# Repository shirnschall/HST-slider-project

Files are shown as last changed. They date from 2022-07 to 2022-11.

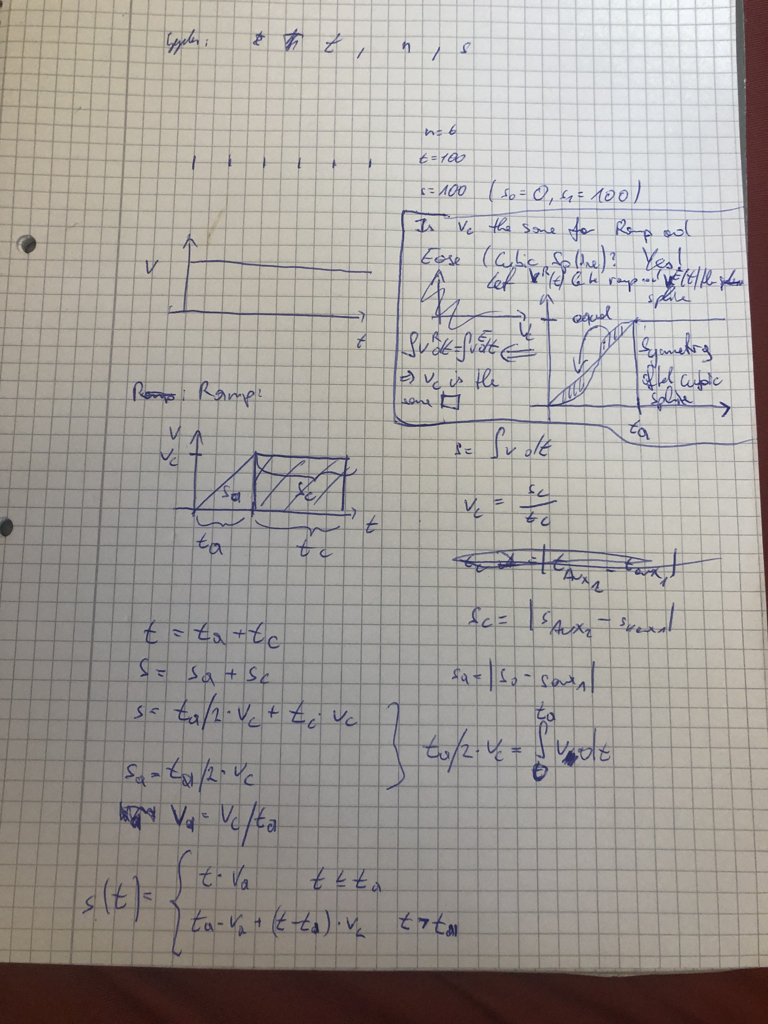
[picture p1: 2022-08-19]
notes-sketches-other-thoughts/non-constant-slider-motion.JPG

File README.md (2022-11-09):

# hs-slider-project
Combining 3d printed and metal parts to build an open source motorized dslr slider.

### More Details
You can find more inforamtion about important features, and how this project was designed in this projects blog post at [https://blog.hirnschall.net/diy-motorized-slider/](https://blog.hirnschall.net/diy-motorized-slider/)

### IMPORTANT NOTE: 
Known issues for pcb v1.0:
- Due to an issue with the current pcb design v1.0 (missing trace), it is required to solder the MS1_PIN to the MS2_PIN on the A4988 stepper driver, to get 8x and 16x micro-stepping working. These pins are labeled on the slider-controller pcb.
- The pinout of the 3.3V regulator ist not correct. The 5V IN and the 3.3V OUT pins have to be swaped. The correct pinout of the pcb is as shown here https://github.com/shirnschall/hs-slider-project/blob/master/schematics/board.pdf

Sorry for the inconvenience!

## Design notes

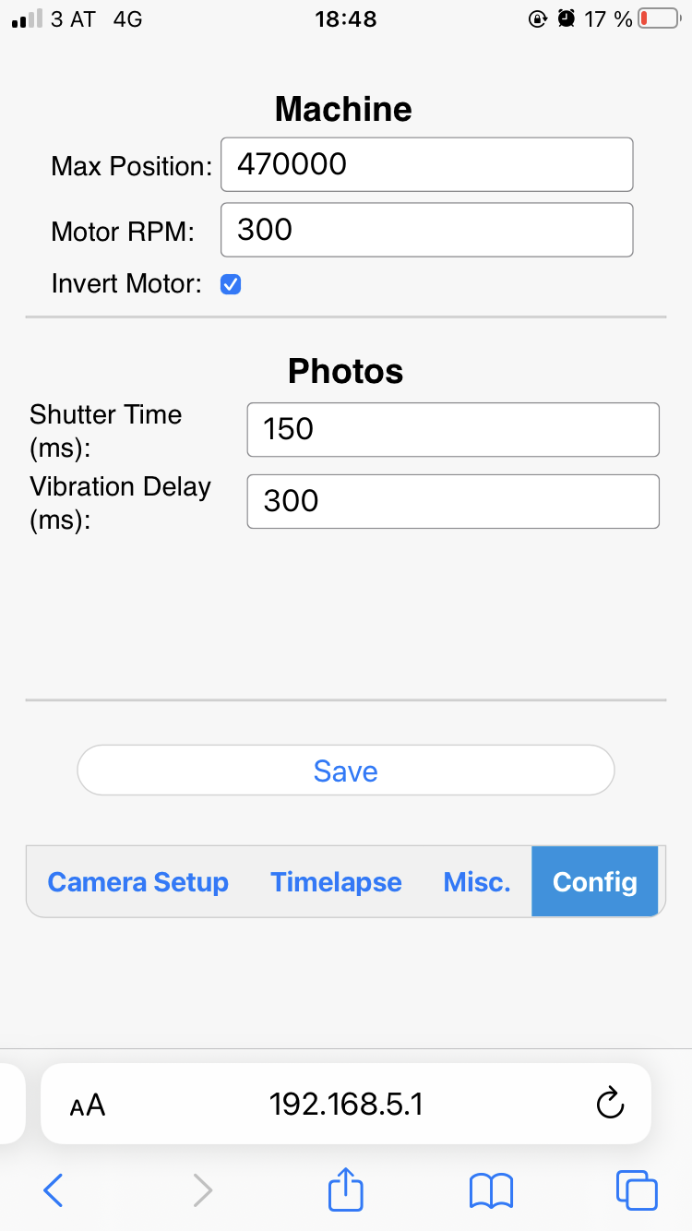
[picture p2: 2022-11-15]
slider-firmware/default-settings.PNG

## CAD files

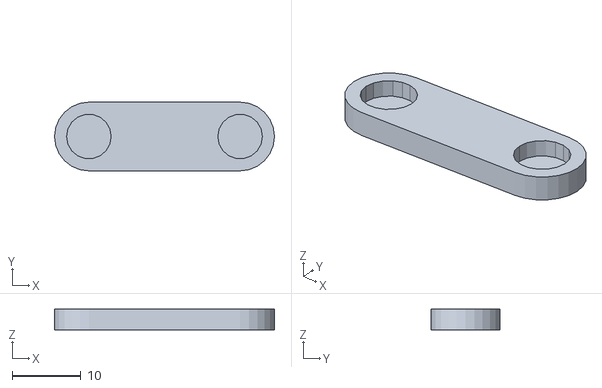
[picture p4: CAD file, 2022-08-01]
stl/belt-mount.stl
32.0 x 10.0 x 3.00

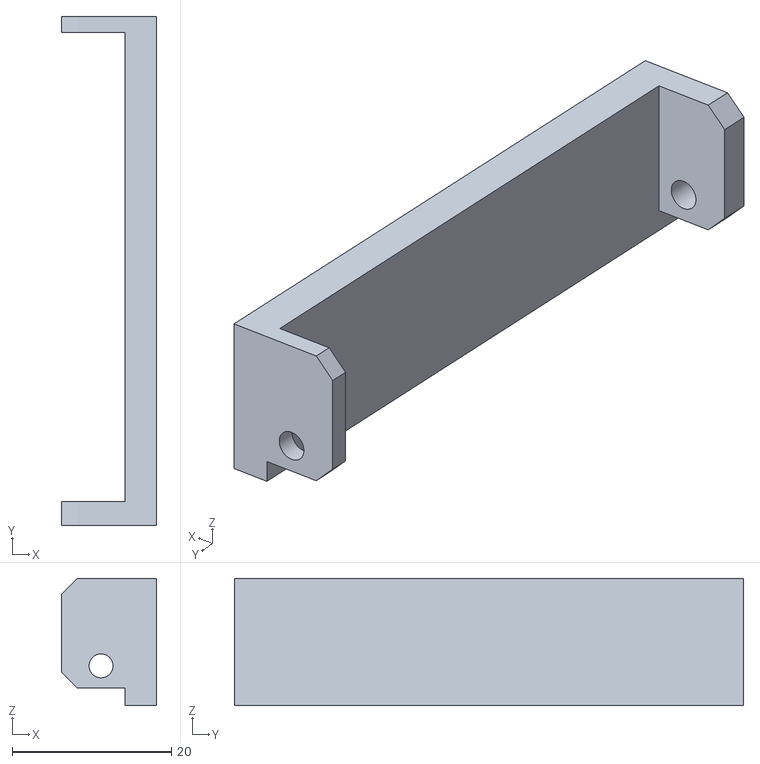
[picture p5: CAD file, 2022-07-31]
stl/pcb-cover.stl
12.0 x 64.0 x 16.0

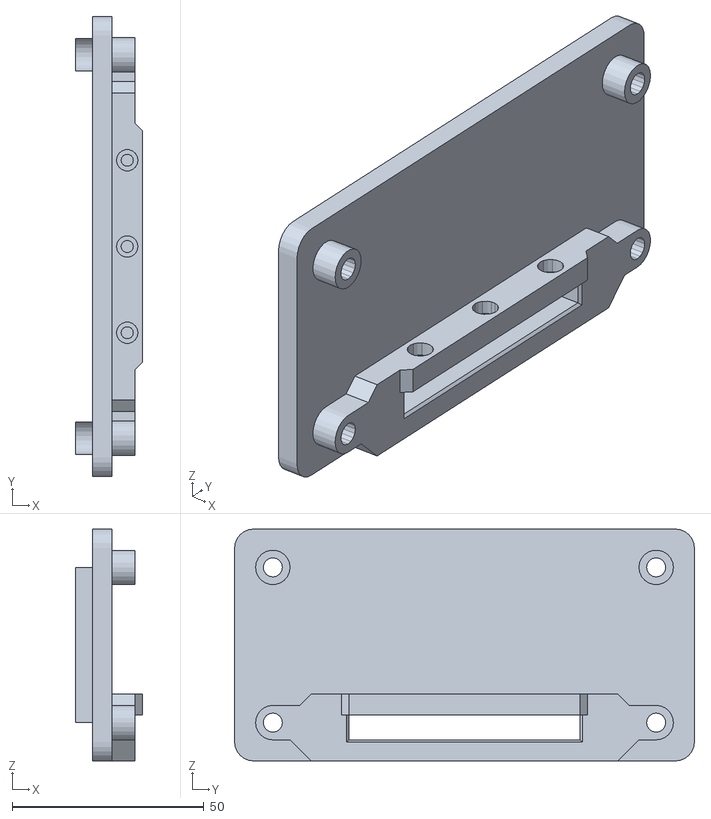
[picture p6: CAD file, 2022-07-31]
stl/tripod-gantry-side.stl
17.5 x 120.0 x 60.5

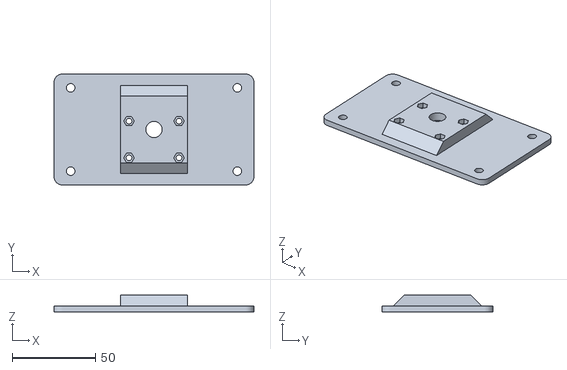
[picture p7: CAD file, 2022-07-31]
stl/cam-gantry-bottom.stl
120.0 x 66.5 x 10.0

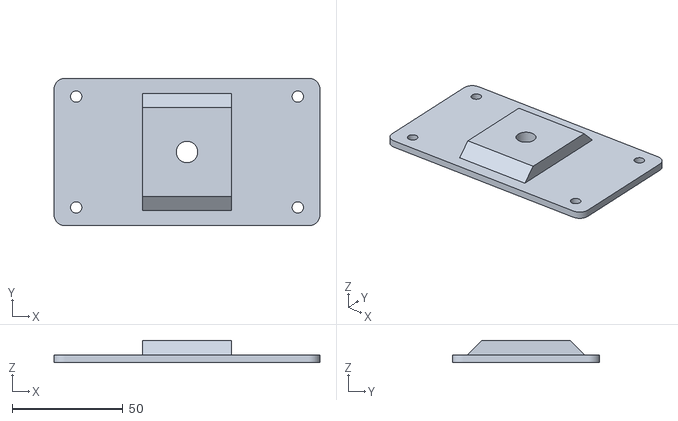
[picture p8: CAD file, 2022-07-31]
stl/cam-gantry-top.stl
120.0 x 66.5 x 10.0

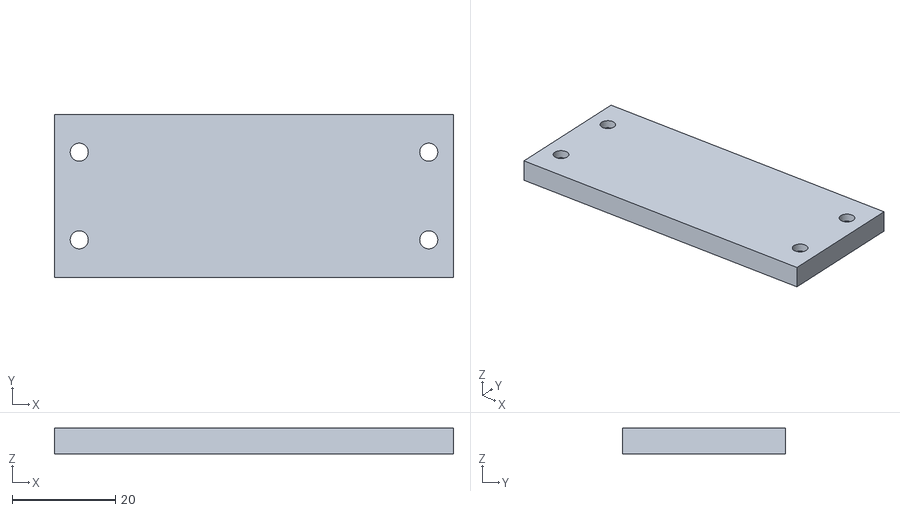
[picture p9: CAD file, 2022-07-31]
stl/idler-cover.stl
77.4 x 31.6 x 5.00

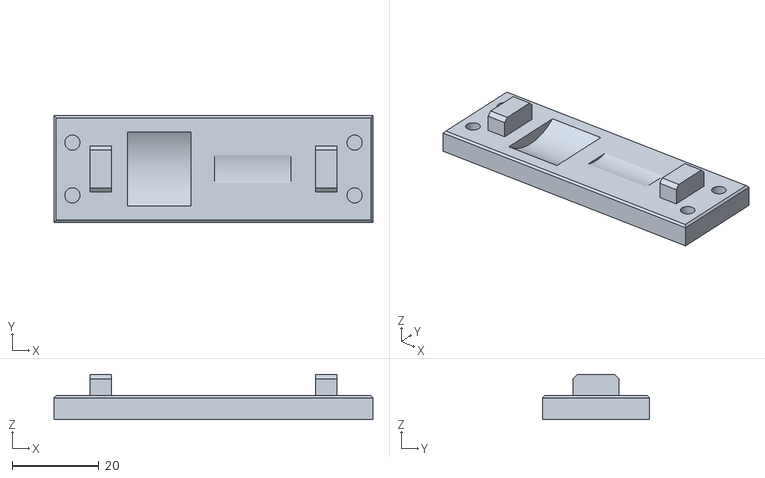
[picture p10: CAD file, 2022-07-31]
stl/motor-end-cover.stl
73.5 x 24.6 x 10.4

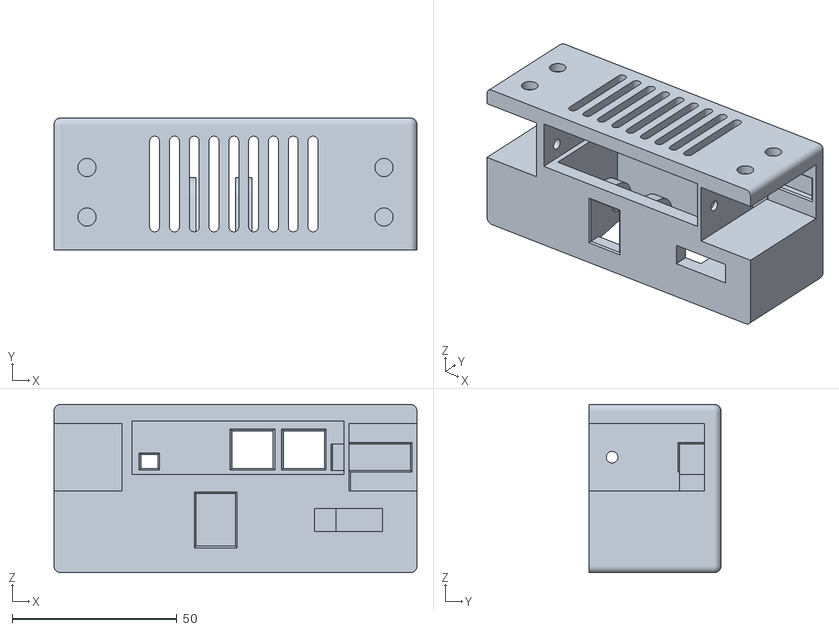
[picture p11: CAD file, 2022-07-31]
stl/pcb-end.stl
110.0 x 40.0 x 51.0

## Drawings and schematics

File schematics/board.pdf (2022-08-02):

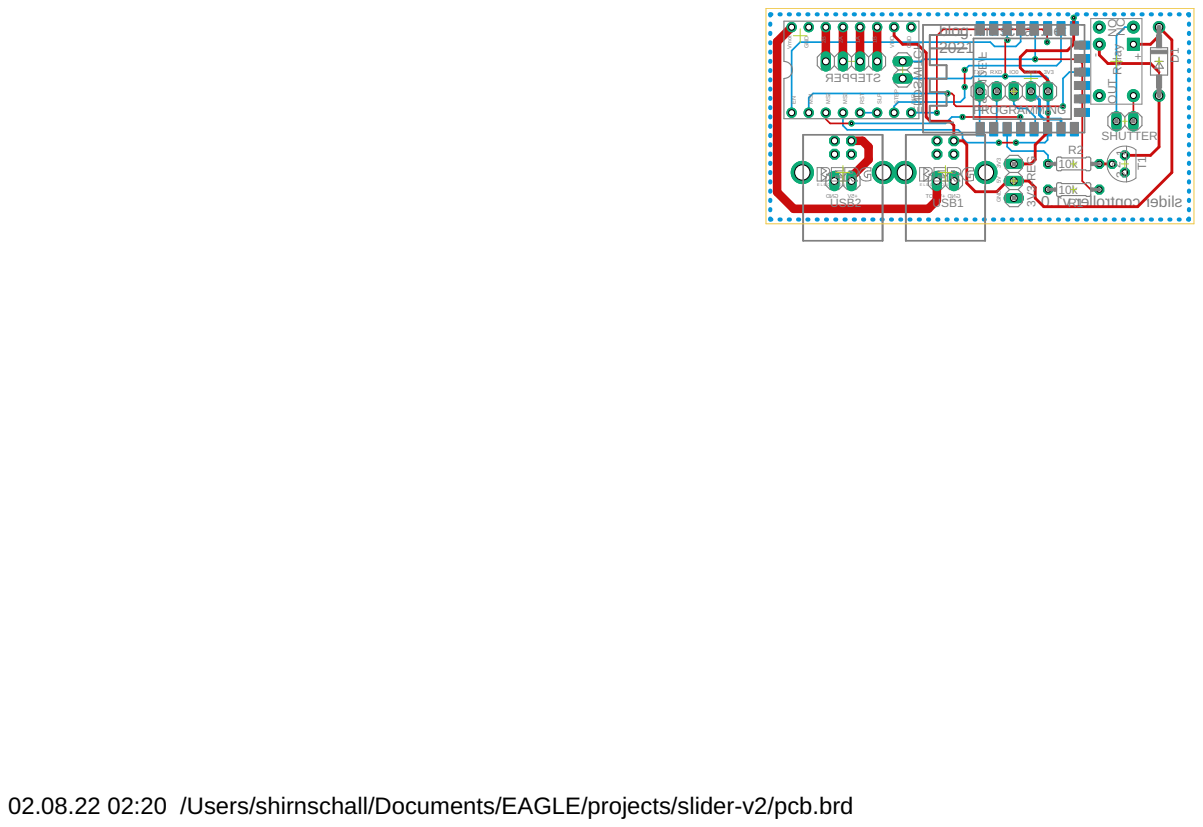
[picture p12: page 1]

02.08.22 02:20 /Users/shirnschall/Documents/EAGLE/projects/slider-v2/pcb.brd

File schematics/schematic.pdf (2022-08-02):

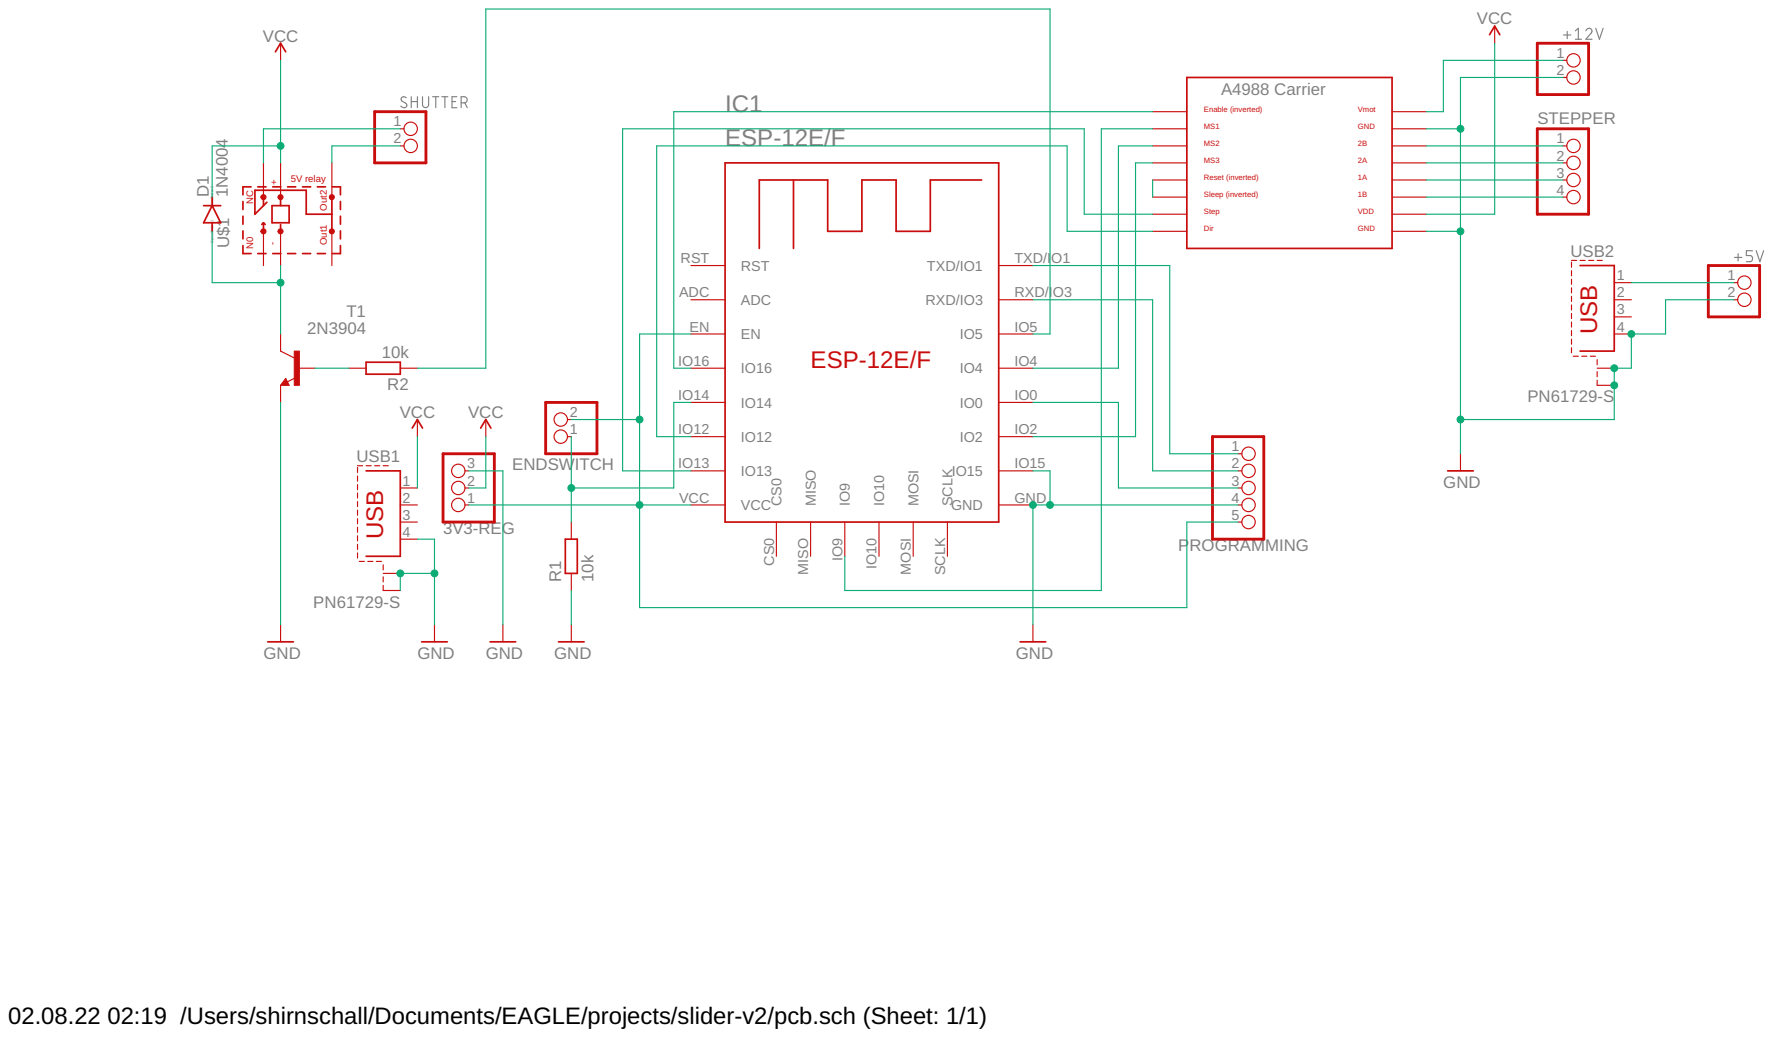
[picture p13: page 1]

02.08.22 02:19 /Users/shirnschall/Documents/EAGLE/projects/slider-v2/pcb.sch (Sheet: 1/1)

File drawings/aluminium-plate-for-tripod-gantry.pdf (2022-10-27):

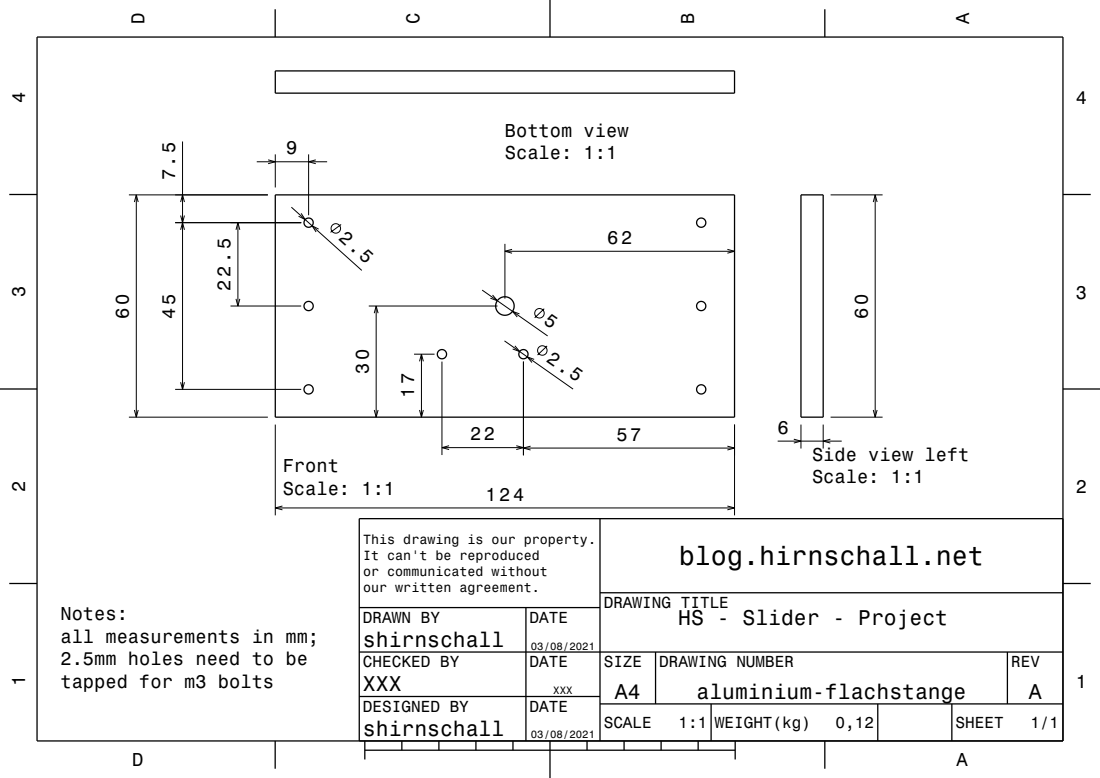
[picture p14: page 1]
Scale: 1:1; Side view left Scale: 1:1; Bottom view Scale: 1:1

This drawing is our property.
It can't be reproduced
or communicated without
our written agreement.

blog.hirnschall.net

DRAWING TITLE
HS - Slider - Project

Notes:
all measurements in mm;
2.5mm holes need to be
tapped for m3 bolts

DRAWN BY shirnschall | DATE 03/08/2021

CHECKED BY XXX | DATE XXX | SIZE A4 | DRAWING NUMBER aluminium-flachstange | REV A

DESIGNED BY shirnschall | DATE 03/08/2021

SCALE 1:1 | WEIGHT(kg) 0,12 | SHEET 1/1

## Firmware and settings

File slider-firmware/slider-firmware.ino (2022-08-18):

#include <EEPROM.h>
//---------------------------------------------------
#include <ESP8266WiFi.h>
const char *ssid = "HS-Slider";
const char *password = "Sebastian012";
IPAddress localIp(192,168,5,1);
IPAddress gateway(192,168,5,1);
IPAddress subnet(255,255,255,0);
//---------------------------------------------------
#include <ESP8266WebServer.h>
ESP8266WebServer server(80);  //listen to port 80
//---------------------------------------------------
#include <Arduino.h>
#include "BasicStepperDriver.h"
// Motor steps per revolution. Most steppers are 200 steps or 1.8 degrees/step
#define MOTOR_STEPS 200
//#define motorRpm 250
#define stepperDir_PIN 12
#define STEPPER_STEP_PIN 13
#define MICROSTEPS 8
#define MS1_PIN 9
#define MS2_PIN 4
#define MS3_PIN 2
#define STEPPER_EN_PIN 16
BasicStepperDriver stepper(MOTOR_STEPS, stepperDir_PIN, STEPPER_STEP_PIN);

//#define shutterDelay 100 //time for the ralay to open
#define RELAY_PIN 5
//#define vibrationDelay 300 //in ms

#define ENDSTOP_PIN 14
//#define stepperDir -1 //-1 or 1 to change direction
//#define maxPos 440000  //in steps
#define HOMING_SPEED 5


//minified with https://kangax.github.io/html-minifier/
//use option "Case sensitive" and disable "remove optional tags", and "remove tag whitespace"
const char index_html[] PROGMEM = R"rawliteral(<!doctype html><html lang="en"><head><link rel="manifest" href="/manifest.webmanifest"><script type="text/javascript">var width=screen.width,meta=document.createElement("meta");meta.name="viewport",meta.content=width<600?"width=device-width,initial-scale="+width/540:"width=device-width,initial-scale=1",document.getElementsByTagName("head")[0].appendChild(meta)</script><style>.slidecontainer{margin:auto;transition:color .2s ease-in-out}.slidecontainer input{position:relative;width:200px;margin:0 10px 0 10px}input{font-size:18pt!important}.slidecontainer button{width:60px;height:40px;background:#fff;font-size:24px;border:1px solid #d3d3d3;cursor:pointer;-webkit-appearance:none;margin:0}body{font-size:16pt;font-family:sans-serif}.start-stop{width:420px;height:40px;border-radius:20px;background:#fff;font-size:24px;border:1px solid #d3d3d3;cursor:pointer;-webkit-appearance:none;margin:10px 10px}.config{width:200px;height:40px;border-radius:20px;background:#fff;font-size:24px;border:1px solid #d3d3d3;cursor:pointer;-webkit-appearance:none;margin:10px 10px}button:hover:enabled{background-color:#0094e2;color:#fff}.heading{text-align:center;font-size:20pt;font-weight:700}td{text-align:center}.slider-l{border-bottom-left-radius:20px;border-top-left-radius:20px}.slider-r{border-bottom-right-radius:20px;border-top-right-radius:20px}#container{width:500px;margin:auto;text-align:center;padding:20px 10px 0 10px}table{margin:auto;padding-top:10px}body,html{margin:0;padding:0;width:100%;height:100%;background-color:#f7f7f7}button{touch-action:manipulation}.slider{width:200px;margin:0 10px}.tab{margin-top:20.667px;padding:0;border-radius:0 0 15px 15px;overflow:hidden;border:1px solid #ccc;background-color:#f1f1f1}.tab button{margin:0;font-size:16pt;background-color:inherit;float:left;border:none;outline:0;cursor:pointer;padding:14px 16px;transition:.3s;font-weight:700}.tab button:hover{background-color:#ddd;color:#000}.tab button.active{background-color:#0094e2;color:#fff}.tabcontent{display:none;padding:6px 0;border-top:none;position:relative}.buttonTableContainer{position:absolute;bottom:-20px;width:100%}.buttonTable{width:450px;margin:25px;margin-top:0}.alignL{text-align:left}hr{border:1px solid #ccc}</style></head><body><div id="container"><div id="setup" class="tabcontent"><div class="slidecontainer"><table><tr class="heading"><td colspan="3">Start Position</td></tr><tr><td><button class="slider-l" id="slider-minus-big-1">-5</button><button class="slider-r" id="slider-minus-1">-1</button></td><td><input type="range" min="0" max="100" value="0" class="slider" id="slider-1"></td><td><button class="slider-l" id="slider-plus-1">+1</button><button class="slider-r" id="slider-plus-big-1">+5</button></td></tr><tr><td></td><td><center><div class="slider-value" id="slider-value-1">16</div></center></td><td></td></tr></table></div><hr><div class="slidecontainer"><table><tr class="heading"><td colspan="3">End Position</td></tr><tr><td><button class="slider-l" id="slider-minus-big-2">-5</button><button class="slider-r" id="slider-minus-2">-1</button></td><td><input type="range" min="0" max="100" value="100" class="slider" id="slider-2"></td><td><button class="slider-l" id="slider-plus-2">+1</button><button class="slider-r" id="slider-plus-big-2">+5</button></td></tr><tr><td></td><td><center><div class="slider-value" id="slider-value-2">16</div></center></td><td></td></tr></table></div><hr><div class="slidecontainer"><table><tr class="heading"><td colspan="3">Current Position</td></tr><tr><td><button class="slider-l" id="slider-minus-big-3" onclick="goToMinus(10)">-10</button><button class="slider-r" id="slider-minus-3" onclick="goToMinus(1)">-1</button></td><td><progress id="slider-3" value="32" max="100" class="slider"></progress></td><td><button class="slider-l" id="slider-plus-3" onclick="goToPlus(1)">+1</button><button class="slider-r" id="slider-plus-big-3" onclick="goToPlus(10)">+10</button></td></tr><tr><td></td><td><center><div class="slider-value" id="slider-value-3">16</div></center></td><td></td></tr></table></div><hr><table><tr><td><button class="config" id="gotostart" onclick="goToStart()">Go to Start</button></td><td><button class="config" id="gotoend" onclick="goToEnd()">Go to End</button></td></tr><tr><td><button class="config" id="home" onclick="home()">Home</button></td><td><button class="config" id="takephoto" onclick="takePhoto()">Take Photo</button></td></tr></table></div><div id="timelapse" class="tabcontent"><div class="buttonTableContainer"><table><tr><td><label for="duration">Duration (s):</label></td><td><input type="number" inputmode="numeric" pattern="[0-9]*" id="duration" name="duration"></td></tr><tr><td><label for="noPics">No. Pictures:</label></td><td><input type="number" inputmode="numeric" pattern="[0-9]*" id="noPics" name="noPics"></td></tr></table><hr><table class="buttonTable"><tr><td colspan="2"><button class="start-stop" id="start" onclick="startJob()">Start</button></td></tr></table></div></div><div id="misc" class="tabcontent" style="color:rgba(16,16,16,.3)"><table><tr class="heading"><td colspan="3">Motion Type</td></tr><tr><td class="alignL"><input type="radio" name="motionType" checked value="linear" id="linear" onchange="updateAuxiliarySliders(-1)" disabled><label for="linear">Constant</label></td><td></td><td></td></tr><tr><td class="alignL"><input type="radio" name="motionType" value="easeInOut" id="easeInOut" onchange="updateAuxiliarySliders(2)" disabled><label for="easeInOut">Ease in/out</label></td><td class="alignL"><input type="radio" name="motionType" value="easeIn" id="easeIn" onchange="updateAuxiliarySliders(0)" disabled><label for="easeIn">Ease in</label></td><td class="alignL"><input type="radio" name="motionType" value="easeOut" id="easeOut" onchange="updateAuxiliarySliders(1)" disabled><label for="easeOut">Ease out</label></td></tr><tr><td class="alignL"><input type="radio" name="motionType" value="rampInOut" id="rampInOut" onchange="updateAuxiliarySliders(2)" disabled><label for="rampInOut">Ramp in/out</label></td><td class="alignL"><input type="radio" name="motionType" value="rampIn" id="rampIn" onchange="updateAuxiliarySliders(0)" disabled><label for="rampIn">Ramp in</label></td><td class="alignL"><input type="radio" name="motionType" value="rampOut" id="rampOut" onchange="updateAuxiliarySliders(1)" disabled><label for="rampOut">Ramp out</label></td></tr></table><hr><div class="slidecontainer" id="auxiliarySliderContainer0"><table><tr class="heading"><td colspan="3">Auxiliary Point (in)</td></tr><tr><td><button class="slider-l" id="slider-minus-big-4">-5</button><button class="slider-r" id="slider-minus-4">-1</button></td><td><input type="range" min="0" max="100" value="20" class="slider" id="slider-4"></td><td><button class="slider-l" id="slider-plus-4">+1</button><button class="slider-r" id="slider-plus-big-4">+5</button></td></tr><tr><td></td><td><center><div class="slider-value" id="slider-value-4">20</div></center></td><td></td></tr></table></div><hr><div class="slidecontainer" id="auxiliarySliderContainer1"><table><tr class="heading"><td colspan="3">Auxiliary Point (out)</td></tr><tr><td><button class="slider-l" id="slider-minus-big-5">-5</button><button class="slider-r" id="slider-minus-5">-1</button></td><td><input type="range" min="0" max="100" value="80" class="slider" id="slider-5"></td><td><button class="slider-l" id="slider-plus-5">+1</button><button class="slider-r" id="slider-plus-big-5">+5</button></td></tr><tr><td></td><td><center><div class="slider-value" id="slider-value-5">80</div></center></td><td></td></tr></table></div><div class="buttonTableContainer"><hr><table class="buttonTable"><tr><td colspan="2"><button class="start-stop" id="start" onclick="startJob()" disabled>Start</button></td></tr></table></div></div><div id="config" class="tabcontent"><table><tr class="heading"><td colspan="2">Machine</td></tr><tr><td class="alignL"><label for="maxPos">Max Position:</label></td><td><input type="number" inputmode="numeric" pattern="[0-9]*" id="maxPos" name="maxPos"></td></tr><tr><td class="alignL"><label for="rpm">Motor RPM:</label></td><td><input type="number" inputmode="numeric" pattern="[0-9]*" id="rpm" name="rpm"></td></tr><tr><td class="alignL"><label for="invertMotor">Invert Motor:</label></td><td class="alignL"><input type="checkbox" id="invertMotor" name="invertMotor"></td><td></td></tr></table><hr><table><tr class="heading"><td colspan="2">Photos</td></tr><tr><td class="alignL"><label for="shutter">Shutter Time (ms):</label></td><td><input type="number" inputmode="numeric" pattern="[0-9]*" id="shutter" name="shutter"></td></tr><tr><td class="alignL"><label for="vibration">Vibration Delay (ms):</label></td><td><input type="number" inputmode="numeric" pattern="[0-9]*" id="vibration" name="vibration"></td></tr></table><div class="buttonTableContainer"><hr><table class="buttonTable"><tr><td colspan="2"><button class="start-stop" id="save" onclick="saveConfig()">Save</button></td></tr></table></div></div><div class="tab"><button id="setupButton" class="tablinks active" onclick="openTab(&#34;setup&#34;)">Camera Setup</button> <button id="timelapseButton" class="tablinks" onclick="openTab(&#34;timelapse&#34;)">Timelapse</button> <button id="miscButton" class="tablinks" onclick="openTab(&#34;misc&#34;)">Misc.</button> <button id="configButton" class="tablinks" onclick="openTab(&#34;config&#34;)">Config</button></div></div><script>function startJob(){dur=document.getElementById("duration").value.toString(),noPics=document.getElementById("noPics").value.toString(),""==dur||""==noPics||"0"==dur||"0"==noPics?alert("Duration and Number of Pictures cannot be none!"):window.location.replace("?start&pos1="+slider[0].value+"&pos2="+slider[1].value+"&duration="+dur+"&nopics="+noPics)}function home(){dur=document.getElementById("duration").value.toString(),noPics=document.getElementById("noPics").value.toString();var e=new XMLHttpRequest;e.open("GET","?home&pos1="+slider[0].value+"&pos2="+slider[1].value+"&duration="+dur+"&nopics="+noPics,!0),e.send(),refresh()}function goToStart(){dur=document.getElementById("duration").value.toString(),noPics=document.getElementById("noPics").value.toString();var e=new XMLHttpRequest;e.open("GET","?gotopos="+slider[0].value+"&pos1="+slider[0].value+"&pos2="+slider[1].value+"&duration="+dur+"&nopics="+noPics,!0),e.send(),refresh()}function goToEnd(){dur=document.getElementById("duration").value.toString(),noPics=document.getElementById("noPics").value.toString();var e=new XMLHttpRequest;e.open("GET","?gotopos="+slider[1].value+"&pos1="+slider[0].value+"&pos2="+slider[1].value+"&duration="+dur+"&nopics="+noPics,!0),e.send(),refresh()}function goToPlus(e){dur=document.getElementById("duration").value.toString(),noPics=document.getElementById("noPics").value.toString();var t=new XMLHttpRequest;t.open("GET","?gotoplus="+e+"&pos1="+slider[0].value+"&pos2="+slider[1].value+"&duration="+dur+"&nopics="+noPics,!0),t.send(),refresh()}function goToMinus(e){dur=document.getElementById("duration").value.toString(),noPics=document.getElementById("noPics").value.toString();var t=new XMLHttpRequest;t.open("GET","?gotominus="+e+"&pos1="+slider[0].value+"&pos2="+slider[1].value+"&duration="+dur+"&nopics="+noPics,!0),t.send(),refresh()}function takePhoto(){dur=document.getElementById("duration").value.toString(),noPics=document.getElementById("noPics").value.toString();var e=new XMLHttpRequest;e.open("GET","?takephoto&pos1="+slider[0].value+"&pos2="+slider[1].value+"&duration="+dur+"&nopics="+noPics,!0),e.send(),refresh()}function refreshCurrentPos(){var e=new XMLHttpRequest;e.onreadystatechange=function(){4==this.readyState&&200==this.status&&(document.getElementById("slider-3").value=parseFloat(this.responseText),document.getElementById("slider-value-3").innerHTML=parseFloat(this.responseText))},e.open("GET","?currentpos",!0),e.send()}function getInitialUIValues(){var e=new XMLHttpRequest;e.onreadystatechange=function(){4==this.readyState&&200==this.status&&(document.getElementById("slider-1").value=parseFloat(this.responseText),document.getElementById("slider-value-1").innerHTML=parseFloat(this.responseText))},e.open("GET","?pos1",!0),e.send();var t=new XMLHttpRequest;t.onreadystatechange=function(){4==this.readyState&&200==this.status&&(document.getElementById("slider-2").value=parseFloat(this.responseText),document.getElementById("slider-value-2").innerHTML=parseFloat(this.responseText))},t.open("GET","?pos2",!0),t.send();var n=new XMLHttpRequest;n.onreadystatechange=function(){4==this.readyState&&200==this.status&&(document.getElementById("noPics").value=parseFloat(this.responseText))},n.open("GET","?nopics",!0),n.send();var s=new XMLHttpRequest;s.onreadystatechange=function(){4==this.readyState&&200==this.status&&(document.getElementById("duration").value=parseFloat(this.responseText))},s.open("GET","?duration",!0),s.send()}function refresh(){var e=new XMLHttpRequest;e.onreadystatechange=function(){4==this.readyState&&200==this.status&&(document.getElementById("slider-3").value=parseFloat(this.responseText),document.getElementById("slider-value-3").innerHTML=parseFloat(this.responseText))},e.open("GET","?currentpos",!0),e.send();var t=new XMLHttpRequest;t.onreadystatechange=function(){4==this.readyState&&200==this.status&&(document.getElementById("maxPos").value=parseFloat(this.responseText))},t.open("GET","?maxpos",!0),t.send();var n=new XMLHttpRequest;n.onreadystatechange=function(){4==this.readyState&&200==this.status&&(document.getElementById("rpm").value=parseFloat(this.responseText))},n.open("GET","?rpm",!0),n.send();var s=new XMLHttpRequest;s.onreadystatechange=function(){4==this.readyState&&200==this.status&&(document.getElementById("invertMotor").checked=!(0<parseFloat(this.responseText)))},s.open("GET","?invertmotor",!0),s.send();var i=new XMLHttpRequest;i.onreadystatechange=function(){4==this.readyState&&200==this.status&&(document.getElementById("shutter").value=parseFloat(this.responseText))},i.open("GET","?shutter",!0),i.send();var d=new XMLHttpRequest;d.onreadystatechange=function(){4==this.readyState&&200==this.status&&(document.getElementById("vibration").value=parseFloat(this.responseText))},d.open("GET","?vibration",!0),d.send()}function saveConfig(){var e=document.getElementById("invertMotor").checked?-1:1,t=new XMLHttpRequest;t.open("GET","?setmaxpos="+document.getElementById("maxPos").value+"&setrpm="+document.getElementById("rpm").value+"&setinvertmotor="+e+"&setshutter="+document.getElementById("shutter").value+"&setvibration="+document.getElementById("vibration").value,!0),t.send()}function openTab(e){refresh();var t=["setup","timelapse","misc","config"],n=4;document.getElementById(e).style.display="block",document.getElementById(e+"Button").className+=" active",document.getElementById(e+"Button").className=document.getElementById(e+"Button").className.replace(" active active"," active");for(var s=0;s<n;++s)t[s]!=e&&(document.getElementById(t[s]).style.display="none",document.getElementById(t[s]+"Button").className=document.getElementById(t[s]+"Button").className.replace(" active",""))}function setDivHeight(){for(var e=["setup","timelapse","misc","config"],t=4,n=document.getElementById("setup").offsetHeight-12-1,s=0;s<t;++s)document.getElementById(e[s]).style.height=n+"px"}function updateAuxiliarySliders(e){-1==e?(disableAuxiliarySlider(0),disableAuxiliarySlider(1)):0==e?(enableAuxiliarySlider(0),disableAuxiliarySlider(1)):1==e?(disableAuxiliarySlider(0),enableAuxiliarySlider(1)):2==e&&(enableAuxiliarySlider(0),enableAuxiliarySlider(1))}function disableAuxiliarySlider(e){0==e?(document.getElementById("slider-4").setAttribute("disabled",!0),document.getElementById("slider-minus-big-4").setAttribute("disabled",!0),document.getElementById("slider-minus-4").setAttribute("disabled",!0),document.getElementById("slider-plus-big-4").setAttribute("disabled",!0),document.getElementById("slider-plus-4").setAttribute("disabled",!0),document.getElementById("auxiliarySliderContainer0").style.color="rgba(16, 16, 16, 0.3)"):1==e&&(document.getElementById("slider-5").setAttribute("disabled",!0),document.getElementById("slider-minus-big-5").setAttribute("disabled",!0),document.getElementById("slider-minus-5").setAttribute("disabled",!0),document.getElementById("slider-plus-big-5").setAttribute("disabled",!0),document.getElementById("slider-plus-5").setAttribute("disabled",!0),document.getElementById("auxiliarySliderContainer1").style.color="rgba(16, 16, 16, 0.3)")}function enableAuxiliarySlider(e){0==e?(document.getElementById("slider-4").removeAttribute("disabled"),document.getElementById("slider-minus-big-4").removeAttribute("disabled"),document.getElementById("slider-minus-4").removeAttribute("disabled"),document.getElementById("slider-plus-big-4").removeAttribute("disabled"),document.getElementById("slider-plus-4").removeAttribute("disabled"),document.getElementById("auxiliarySliderContainer0").style.color="#000"):1==e&&(document.getElementById("slider-5").removeAttribute("disabled"),document.getElementById("slider-minus-big-5").removeAttribute("disabled"),document.getElementById("slider-minus-5").removeAttribute("disabled"),document.getElementById("slider-plus-big-5").removeAttribute("disabled"),document.getElementById("slider-plus-5").removeAttribute("disabled"),document.getElementById("auxiliarySliderContainer1").style.color="#000")}for(var slider=[],sliderValues=[],sliderC=2,smallIncrement=1,bigIncrement=5,i=0;i<sliderC;++i)slider.push(document.getElementById("slider-"+(i+1))),sliderValues.push(document.getElementById("slider-value-"+(i+1))),sliderValues[i].innerHTML=slider[i].value,function(t){slider[t].oninput=function(e){sliderValues[t].innerHTML=slider[t].value}}(i),function(t){document.getElementById("slider-minus-"+(t+1)).onclick=function(e){slider[t].value=parseFloat(slider[t].value)-smallIncrement,sliderValues[t].innerHTML=slider[t].value}}(i),function(t){document.getElementById("slider-minus-big-"+(t+1)).onclick=function(e){slider[t].value=parseFloat(slider[t].value)-bigIncrement,sliderValues[t].innerHTML=slider[t].value}}(i),function(t){document.getElementById("slider-plus-"+(t+1)).onclick=function(e){slider[t].value=parseFloat(slider[t].value)+smallIncrement,sliderValues[t].innerHTML=slider[t].value}}(i),function(t){document.getElementById("slider-plus-big-"+(t+1)).onclick=function(e){slider[t].value=parseFloat(slider[t].value)+bigIncrement,sliderValues[t].innerHTML=slider[t].value}}(i);window.setInterval("refreshCurrentPos()",1e3),getInitialUIValues(),refresh(),document.getElementById("setup").style.display="block",setDivHeight(),updateAuxiliarySliders(-1)</script></body></html>
)rawliteral";
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
void loop() {
  //code to find maxPos value
  //int maxsteps=0;
  //while(!digitalRead(ENDSTOP_PIN)){
  //  enableStepper(); //enalbe stepper
  //  maxsteps += 10000;
  //  stepper.move(stepperDir*-10000);
  //  Serial.println(maxsteps);
  //  delay(500);
  //}
  
  //check if job is running, if so handle timer, movement, and shutter
  if(currentStatus=='s' && currentPhoto>= numberPhotos){
    if(showDebugOutput)
      Serial.println("Job done");
    currentStatus='i';
  }
  else if(currentStatus=='s'){ //job running
    //check if time since last photo is larger than photoInterval
    if(millis() - lastPhotoTime + timeToMove  > photoInterval){
      if(showDebugOutput)
        Serial.println("moving to new location");
      lastPhotoTime=millis();
      //move to position
      timeToMove = millis();
      goToPos(currentPos + photoSteps);
      timeToMove = millis()-timeToMove;
      //delay to avoid vibrations
      if(showDebugOutput)
        Serial.println("vibration delay");
      delay(vibrationDelay);
      if(showDebugOutput)
        Serial.println("photo");
      //take photo
      takePhoto();

      //update stats
      ++currentPhoto;
      disableStepper();
    }
  }


  
  server.handleClient();  //process all the requests for the Webserver
}

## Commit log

2022-08-02 added schematic for custom pcb
2022-08-16 added current pos section, go to buttons and bugfixes for status page
    [slider-firmware.ino]
2022-08-16 v0.2
    -added manual controls as well as current pos readout
    -added go to start/end buttons to simplify setting up the camera
    -store current position to eeprom to save current when powered off
    -switched from reloading page to xhtml request using js to avoid clearing textboxes
    -fixed progressbar on status page
    -fixed status page when a job is finished
    -fixed an issue where the stepper was not disabled after a move, causing increased power usage
    [slider-firmware.ino]
2022-08-16 added take photo button and compressed html files
    -added take photo button to simplify camera setup
    -now using minified html code to reduce memory usage
    -changed default status page progress bar value from 32 to 0
    -changed default response for manual movement GET requests from index_html to currentPos
2022-08-18 completed v0.3.0
    -fixed issue on statuspage as multiple requests hat the same name
    -fixed start button onclick event
    -fixed invert motor checkbox
    -added eeprom save and read functions to store config between restarts
    -switched from define to normal variables to change config using webui
    -known issue when changing chowDebugOutput to 0, workaround: keep it at 1
    - tried to remove eeprom writes. now data is only written to eeprom when a job ends, after a manual move, when config is saved via webui
    [slider-firmware.ino]
2022-10-27 modeled missing holes for belt clamp, added note for unit and which holes to tap
2022-11-15 added endstop wiring diagram
